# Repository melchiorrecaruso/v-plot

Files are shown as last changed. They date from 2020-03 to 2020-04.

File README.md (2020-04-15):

# **vPlot**

**vPlot** is a vertical printer, a kind of printer that draws lines and shapes by moving a pen on a vertical surface using two motors and gravity force.

## **Working principle**

Each pen holder position is defined by two lengths, A and B.

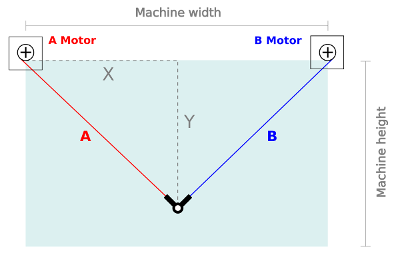
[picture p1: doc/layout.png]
Layout


Each lengths is calculated using Pythagoras' theorem.

Equations

Usually, the motors are positioned at the same height from the ground.

## **Working area**

vPlot-Layout tool calculates best print area dimensions by

>- distance between the two motors
>- min ratio between belt tension and pen holder weigth (default 0.5)
>- max ratio between belt tension and pen holder weigth (default 1.5)
>- max ratio between pen holder displacement and belt length changement (default 1.4)

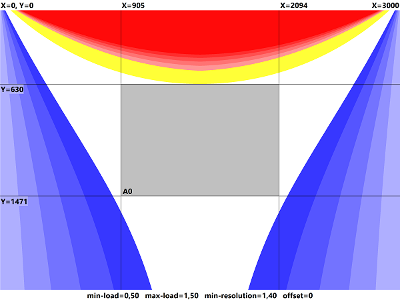
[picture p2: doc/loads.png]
Loads


In the blank area all three parameters are respected. In the blue area the load of once belt is less than the minimum allowed load; In the red zone the tension of once belt is higher than the maximum allowed load; In the yellow area the resolution of the plotter is lower than the minimum allowed resolution.

Generally, than larger is the distance between the two motors, than larger is the area of the white zone.

## **vPlot hardware requirements**

The main components are:

>- 1x Arduino Uno R3 board or Mega 2560 R3
>- 1x CNC Shield V3 expansion board
>- 2x DRV8825 stepper motor driver 
>- 2x Stepper motor Nema-17 (min torque 40Ncm)
>- 1x Micro digital servo 
>- 2x Timing belt pulley GT2 20T 5mmn bore
>- 2x Smooth idler pulley with bearings GT2 20T 5mm bore
>- 2x 2,5m GT2 timming belt 
>- 1x 12V/5A power supplier 
>- 1x Pen holder (print with a 3D printer)
>- 2x Motor supports (print with a 3D printer)

## **vPlot software requirements**

For compiling vPlot-Client use:  

>- [Lazarus IDE and FreePascal compiler](https://www.lazarus-ide.org/index.php?page=downloads)

>- [BGRA Controls Library](https://bgrabitmap.github.io/)

For loading server sketch on arduino board use:

>- [Arduino IDE](https://www.arduino.cc/en/Main/Software)

## **Before assembling**

Set the Vref current on DRV8825 stepper drivers. See the guide

>- [How to control a stepper motor with DRV8825](https://www.makerguides.com/drv8825-stepper-motor-driver-arduino-tutorial/)

## **Connecting to Arduino**

Nema 17 motors have 200 steps for rotation but by enabling microsteps on the Pololu drivers we can obtain up to 3200 steps for rotation which allows for much more precision. For doing that add two jumpers on green pins.

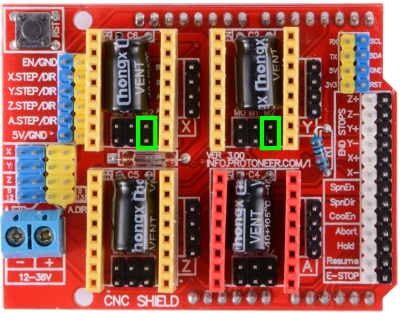
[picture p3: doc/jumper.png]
microsteps (https://)
 

Then
- Mount the two stepper drivers on CNC schield board;
- Connect motors to the green pins;  
- Connect servo-motor to blu pins.

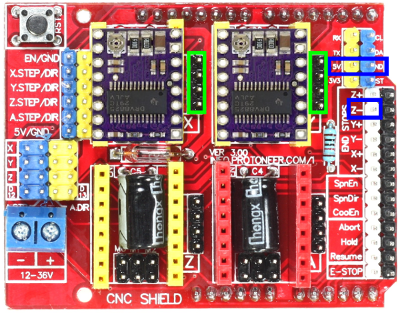
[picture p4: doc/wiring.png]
wiring (https://)
 

- Mount CNC Shield on arduino board;
- Connect Arduino board to PC by usb port and load server sketch.
- Connect 12V power supply to CNC schield;
- Open and use vPlot-Client to control Server

## **LICENSE**

[GNU General Public License v3.0](LICENSE)

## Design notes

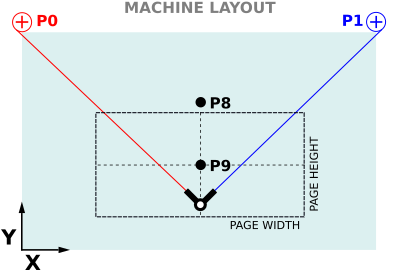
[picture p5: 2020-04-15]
doc/layout3.png

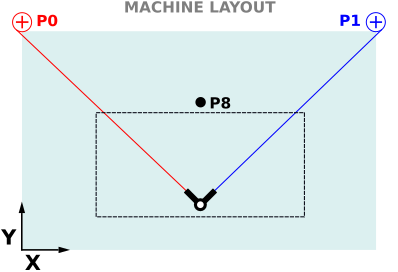
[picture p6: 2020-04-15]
doc/layout2.png

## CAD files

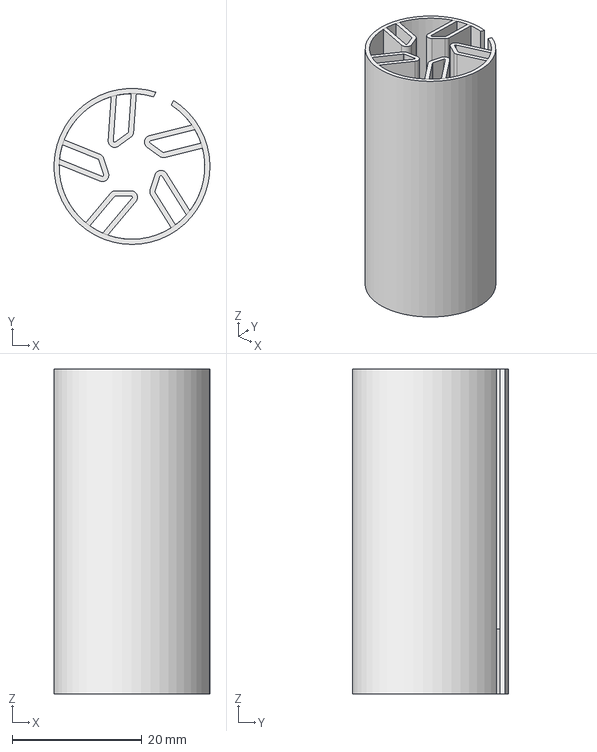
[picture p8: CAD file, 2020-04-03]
hardware/vp5007.FCStd
24.0 x 24.0 x 50.0 mm

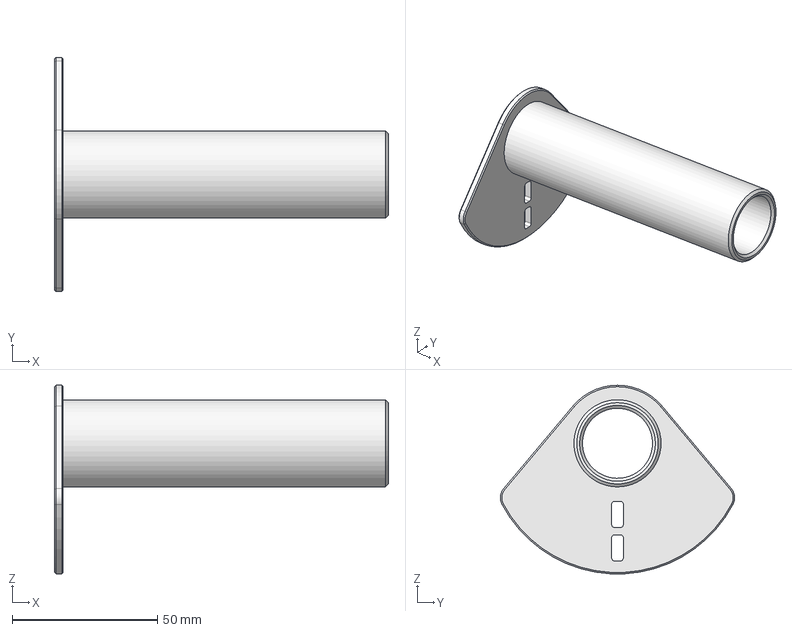
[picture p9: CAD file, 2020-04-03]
hardware/vp5005.FCStd
115.0 x 80.7 x 64.9 mm

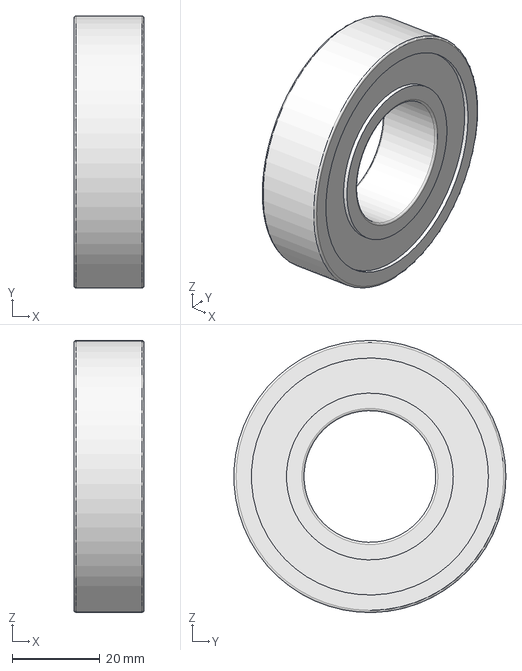
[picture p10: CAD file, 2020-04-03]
hardware/vp5001.FCStd
16.0 x 62.0 x 62.0 mm

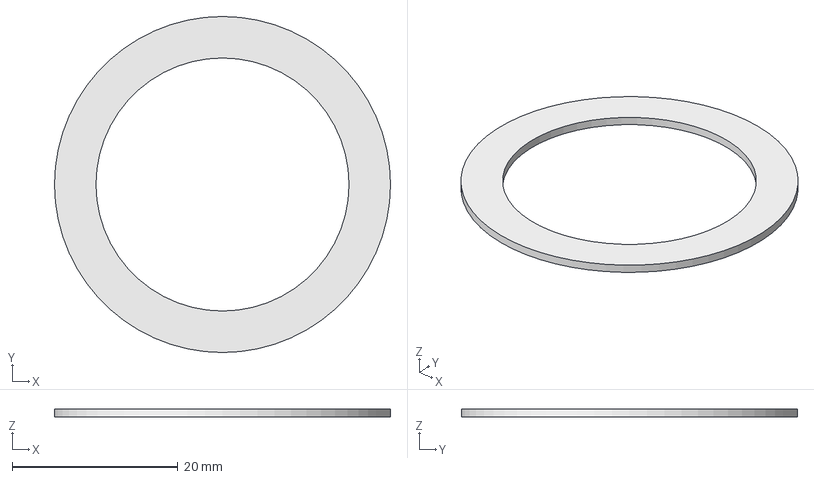
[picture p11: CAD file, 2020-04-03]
hardware/vp5004.FCStd
40.5 x 40.5 x 1.00 mm

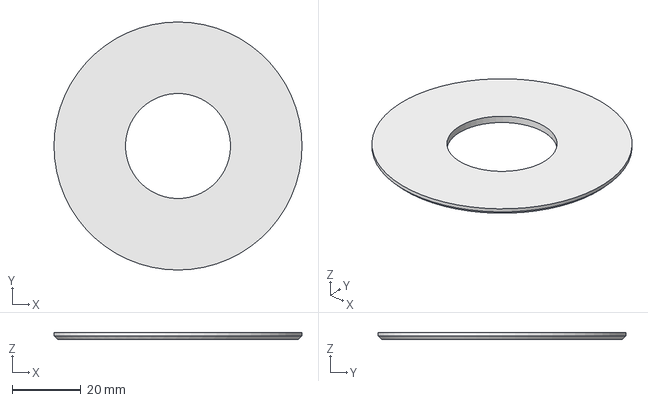
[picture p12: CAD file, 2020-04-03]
hardware/vp5006.FCStd
72.0 x 72.0 x 2.00 mm

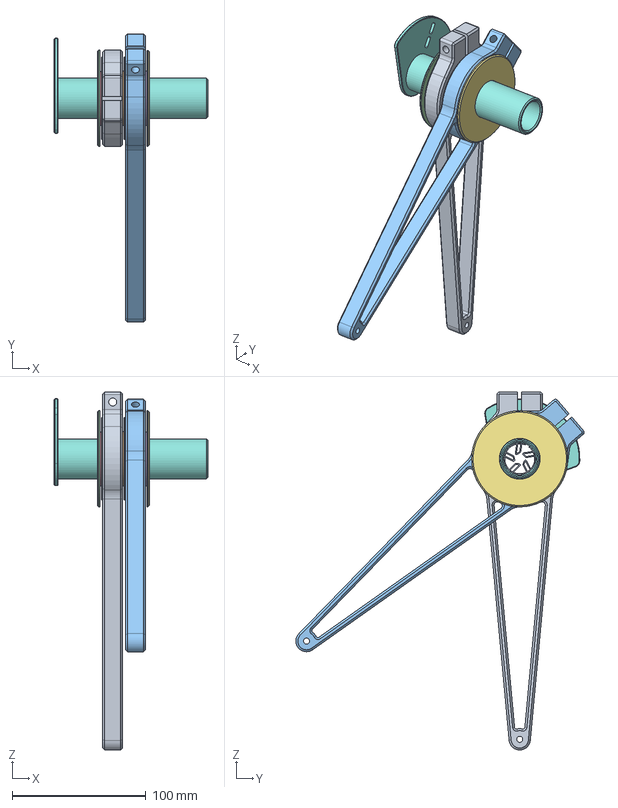
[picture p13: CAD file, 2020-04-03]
hardware/vp5000.FCStd
115.0 x 215.8 x 268.0 mm
vp5003_001
vp5004_001
vp5003_002
vp5006_001
vp5004_002
vp5004_003
vp5006_002
vp5005_001
vp5007_001

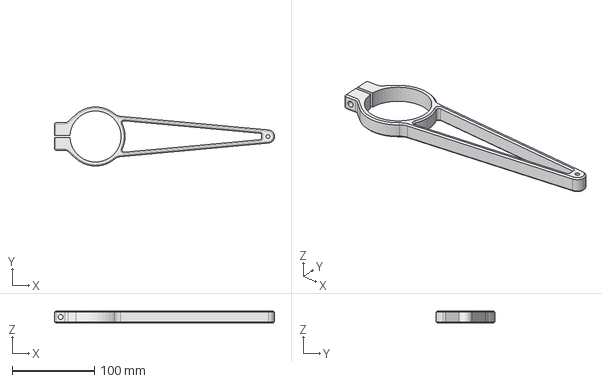
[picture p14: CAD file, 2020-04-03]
hardware/vp5002.FCStd
268.0 x 72.0 x 15.0 mm

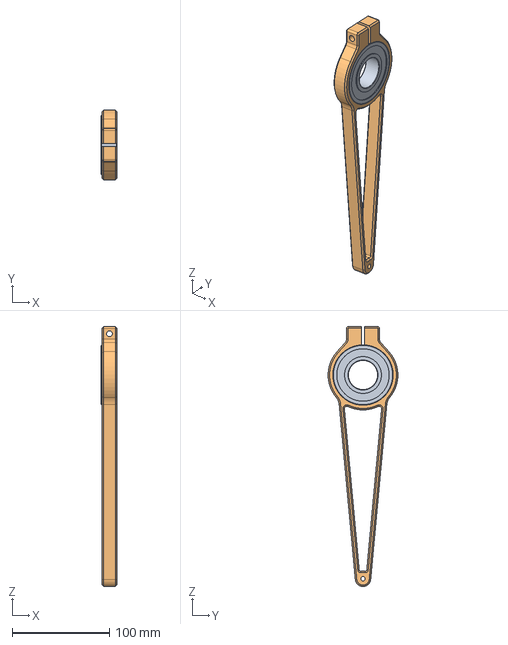
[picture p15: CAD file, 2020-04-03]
hardware/vp5003.FCStd
16.0 x 72.0 x 268.0 mm
vp5001_001
vp5002_001

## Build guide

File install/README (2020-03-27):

vPlot Client 

A simple vertical plotter interface

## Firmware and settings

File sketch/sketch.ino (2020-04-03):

//  vPlotter Server for Arduino Uno R3 board

//  Author:   Melchiorre Caruso
//  Date:     20 November 2019
//  Modified: 03 April    2020

//  Librerie utilizzate nel codice sorgente

#include <math.h>
#include <Servo.h>

// definizione PIN shield CNC V3

#define MOTOR_ONOFF_PIN   8

#define MOTOR_X_STEP_PIN  2
#define MOTOR_X_DIR_PIN   5
#define MOTOR_Y_STEP_PIN  3
#define MOTOR_Y_DIR_PIN   6
#define MOTOR_Z_PIN       11

// definizione costanti protocollo seriale 

#define GETXCOUNT         240
#define GETYCOUNT         241
#define GETZCOUNT         242
#define GETKB             243
#define GETKM             244
#define SETXCOUNT         230
#define SETYCOUNT         231
#define SETZCOUNT         232
#define SETKB             233
#define SETKM             234

// definizione variabili principali

static byte Buffer[128];
static long BufferIndex;
static long BufferSize;
static unsigned long LoopStart;
static unsigned long LoopDelay;
static long RampIndex;
static long RampKB;
static long RampKM;
static long xCount;
static long yCount;
static long zCount;
static long zDelay;

Servo motorZ;

union {
  byte asbytes[4];
  long aslong;
} data;

// Motor xy & z routines

void ExecRamp(byte bt) {  
  if (bitRead(bt, 6) == 1) { RampIndex++; }
  if (bitRead(bt, 7) == 1) { RampIndex--; }
  RampIndex = max(RampKM, RampIndex);
}

void ExecServo(byte bt) {
  long dz = bitRead(bt, 4);
  if (bitRead(bt, 5) == 1) { dz *= -1; }
 
  zCount += dz;
  if (dz != 0) {
    motorZ.write(zCount);
    delay(zDelay);
  }
}

void ExecStepper(byte bt) {
  long dx = bitRead(bt, 0);
  long dy = bitRead(bt, 2);
  if (bitRead(bt, 1) == 1) { dx *= -1; }
  if (bitRead(bt, 3) == 1) { dy *= -1; }

  xCount += dx;
  if (dx < 0) {
    digitalWrite(MOTOR_X_DIR_PIN, HIGH);
  } else {
    digitalWrite(MOTOR_X_DIR_PIN, LOW );
  }

  yCount += dy;
  if (dy < 0) {
    digitalWrite(MOTOR_Y_DIR_PIN, LOW );
  } else {
    digitalWrite(MOTOR_Y_DIR_PIN, HIGH);
  }

  if ((dx != 0) || (dy != 0)) {
    if (dx != 0) { digitalWrite(MOTOR_X_STEP_PIN, HIGH); }
    if (dy != 0) { digitalWrite(MOTOR_Y_STEP_PIN, HIGH); }
    delayMicroseconds(20);

    if (dx != 0) { digitalWrite(MOTOR_X_STEP_PIN, LOW ); }
    if (dy != 0) { digitalWrite(MOTOR_Y_STEP_PIN, LOW ); }
  }
}

void ExecInternal(byte bt) {
  switch (bt) {
    case SETXCOUNT:
      Serial.readBytes(data.asbytes, 4);
      Serial.write(SETXCOUNT);
      xCount = data.aslong;
      break;
    case SETYCOUNT:
      Serial.readBytes(data.asbytes, 4);
      Serial.write(SETYCOUNT);
      yCount = data.aslong;
      break;
    case SETZCOUNT:
      Serial.readBytes(data.asbytes, 4);
      Serial.write(SETZCOUNT);
      zCount = data.aslong;
      break; 
    case SETKB:
      Serial.readBytes(data.asbytes, 4);
      Serial.write(SETKB);
      RampKB = data.aslong;
      break;  
    case SETKM:
      Serial.readBytes(data.asbytes, 4);
      Serial.write(SETKM);
      RampKM = max(1, data.aslong);
      break;                  
    case GETXCOUNT:
      data.aslong = xCount;
      Serial.write(GETXCOUNT);
      Serial.write(data.asbytes, 4);
      break;
    case GETYCOUNT:
      data.aslong = yCount;
      Serial.write(GETYCOUNT);
      Serial.write(data.asbytes, 4);
      break;
    case GETZCOUNT:
      data.aslong = zCount;
      Serial.write(GETZCOUNT);
      Serial.write(data.asbytes, 4);
      break;
    case GETKB:
      data.aslong = RampKB;
      Serial.write(GETKB);
      Serial.write(data.asbytes, 4);
      break;  
    case GETKM:
      data.aslong = RampKM;
      Serial.write(GETKM);
      Serial.write(data.asbytes, 4);
      break;           
    default:
      Serial.write(bt);
      break;      
  }
  RampIndex = RampKM;  
}

// Setup routine

void setup() {
  // init serial
  Serial.begin(115200);
  Serial.setTimeout(1000);
  // clear serial
  while (Serial.available() > 0) {
    Serial.read();
    delay(50);
  }  
  // init stepper X/Y
  pinMode(MOTOR_X_STEP_PIN, OUTPUT);
  pinMode(MOTOR_Y_STEP_PIN, OUTPUT);
  pinMode(MOTOR_X_DIR_PIN,  OUTPUT);
  pinMode(MOTOR_Y_DIR_PIN,  OUTPUT);
  pinMode(MOTOR_ONOFF_PIN,  OUTPUT);
  // enable steppers
  digitalWrite(MOTOR_ONOFF_PIN, LOW);  
  // init servo Z
  motorZ.attach(MOTOR_Z_PIN);
  // init variables
  BufferIndex = 0;
  BufferSize = 0;
  LoopStart = micros();
  LoopDelay = 400;
  RampIndex = 1;
  RampKB = 40000;
  RampKM = 1;
  xCount = 0;
  yCount = 0;
  zCount = motorZ.read();
  zDelay = 5;  
}

// Main Loop

void loop() {
  if ((unsigned long)(micros() - LoopStart) >= LoopDelay) {
    LoopStart = micros();
    if (BufferIndex == BufferSize) {
      BufferIndex = 0;
      BufferSize = Serial.available();
      if (BufferSize > 0) {
        Serial.readBytes(Buffer, BufferSize);
        Serial.write(BufferSize);
      }
    }

    if (BufferIndex < BufferSize) {
      byte bt = Buffer[BufferIndex];
      if (bt < B11000000) {
        ExecRamp(bt);
        ExecServo(bt);
        ExecStepper(bt);
      } else {
        ExecInternal(bt);
      }
      BufferIndex++;          
    }   
    LoopDelay = round(RampKB*(sqrt(RampIndex+1)-sqrt(RampIndex)));
  }
}

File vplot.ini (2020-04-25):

[LAYOUT]
POINT0.X=0
POINT0.Y=2200
POINT1.X=2566
POINT1.Y=2200
POINT8.X=1283
POINT8.Y=1339
POINT9.OFFSET=-10
POINT9.FACTOR=-0.5

[PULLEY-0]
RADIUS=6
RATIO=0.012485

[PULLEY-1]
RADIUS=6
RATIO=0.012485

[SERVO-Z]
VALUE-0=170
VALUE-1=135
VALUE-2=115

[PAGE]
HEIGHT=841
WIDTH=1189

[RAMP]
KB=40000
KL=200
KM=10

[WAVE]
POINT0.X=0
POINT0.Y=0
POINT1.X=0
POINT1.Y=0
POINT2.X=0
POINT2.Y=0
POINT3.X=0
POINT3.Y=0
POINT4.X=0
POINT4.Y=0
POINT5.X=0
POINT5.Y=0
POINT6.X=0
POINT6.Y=0
POINT7.X=0
POINT7.Y=0
POINT8.X=0
POINT8.Y=0
SCALE=1
OFF=1

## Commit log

2020-01-04 First upload
    vplot for arduino, firmware and app.
2020-01-04 added ramp diagrams
    [ramps.ods]
2020-01-08 Pen raising when driver is killed
2020-01-13 Updated driver unit
    -new error message
    -updated sync routine
2020-01-21 New driver ramp routine
2020-01-21 Updated Ramp files
    [ramps.ods]
2020-03-31 Updated wiring.png
2020-04-03 Added pen holder files
    [vp5000.FCStd, vp5001.FCStd, vp5002.FCStd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]
2020-04-05 Reload setting file on calibration
2020-04-15 Updated ramps file
    [ramps.ods]
2020-04-19 Added third servo-z position
2020-04-25 vpserial: power consumption bugfix
    [vplot.ini]
